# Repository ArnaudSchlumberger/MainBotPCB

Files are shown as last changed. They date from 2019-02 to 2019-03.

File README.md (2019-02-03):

# MainBotPCB

This project is part of Robot Télécom Strasbourg's work as part of our participation to the French Robot Cup.

See our Github page here: https://github.com/AssociationRobotTelecomStrasbourg

And our website (quite empty yet :/ ) here :https://associationrobottelecomstrasbourg.github.io/

MainBotPCB is the PCB that will contain the majority of the  components and connections required for our main robot to work, hence the original name :) .

NotesConception.md contains my notes while working on this project (in French)

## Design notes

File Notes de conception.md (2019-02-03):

##Cahier des charges 

##Carte de contrôle robot principal

Liste rapide des impératifs :

Accueillir carte Teensy 3.6

Maintenir une flexibilité sur la carte :

    • Pins femelle pour la Teensy
    
Communication avec d’autres composants :

    • Bus i2c
    
        ◦ Encodeurs
        
        ◦ Communication avec plusieurs composants (capteurs)
        
            ▪ Multiplexeur
            
Alimentation :

    • Régulateur 3,3V : pour Teensy et pour les composants
    
Connexion à Raspberry Pi : quelles informations ?

Ascenseur : Moteurs pas à pas 

Drivers moteurs :

https://www.robotshop.com/eu/fr/controleur-un-moteur-13a-5-a-30v-cytron.html

Datasheet :https://www.robotshop.com/media/files/pdf2/cyt-132-v2.3.pdf

Pilotés directement par PWM par la Teensy.

Encodeurs :

Communication par bus I2C

Servomoteurs/Moteurs pas à pas :

	Comment communiquer avec ? 
	
		→ PWM

Branchement Teensy en SMD :

Avec des headers males soudés sur les connexions SMD :

https://www.molex.com/molex/products/datasheet.jsp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

Cette série de headers est la bonne.

Avec des pogos :

Il faut s’assurer que les hauteurs soient bonnes pour avoir des bons contacts.

Avec ces pogos :https://www.mouser.fr/datasheet/2/273/009.1-1022823.pdf

Il faut réduire la hauteur des headers femelles, d’où :
Headers femelles : 

	Schematics https://www.molex.com/pdm_docs/sd/448120024_sd.pdf 
	
	Datasheet :https://www.mouser.fr/datasheet/2/276/0448120024_PCB_RECEPTACLES-146024.pdf
	
	Shop link:https://www.mouser.fr/ProductDetail/Molex/44812-0024?qs=sGAEpiMZZMs%252bGHln7q6pmxAVkKtOEC39IGv%2fKV14Mac%3d

Communication entre microcontrôleurs et autres trucs :

	Le robot sera embarqué d’une R.Pi qui s’occupera de la vision. Comment échanger les informations entre les deux ? En considérant la Teensy comme le Master de tout le robot, il faut configurer la R.Pi en Slave. 
Une piste ici : https://raspberrypi.stackexchange.com/questions/76109/raspberry-as-an-i2c-slave
Étendons la question à l’ensemble des composants du robot : La Teensy doit-elle contrôler l’ensemble du robot directement et simultanément, ou bien utiliser un ensemble de Slaves I2C ?
Teensy un peu overkill pour un simple chef d’orchestre ?
L’idée est à tester : communication entre deux Arduinos et commande de l’une par une autre.

Attention à la compatibilité des niveaux logiques d’un microcontrôleur à un autre :

	Pour une Arduino, la tension de niveau haut logique est de 5V, alors que celle-ci est de 3.3V pour une Rpi. Une Arduino comprend le 3.3V, mais il est dangereux de communiquer en 5V avec la Rpi. Il faut donc effectuer une conversion de niveaux logiques de bus I2C.

Il existe des convertisseurs de niveaux logiques, petite vidéo :https://www.youtube.com/watch?v=7N1shxJ8k7I

Mais on peut se contenter d’utiliser une diode Zener en inverse pour limiter la tension de communication à 3.3V. Cette diode (1N4728) pourrait faire l’affaire: https://components101.com/sites/default/files/component_datasheet/3.3V-Zener-Diode-1N4728A-datasheet.pdf

Communication I2C Arduino/Arduino :
https://www.instructables.com/id/I2C-between-Arduinos/

Ressources :
I2C :
https://www.youtube.com/watch?v=N0YtIzGIW4k
Teensy KiCAD library :
https://github.com/XenGi/teensy_library (schematics)
https://github.com/XenGi/teensy.pretty (footprints)
Teensy pins picture :
https://www.pjrc.com/teensy/card9a_rev1.png

Shop :
Pogo pins :https://www.cfeconn.com/connector/2-54mm-pogo-pin-spring-2-pin-smd-connector-supply
Multiplexeur :https://www.amazon.fr/s/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
https://learn.adafruit.com/adafruit-tca9548a-1-to-8-i2c-multiplexer-breakout/overview

end

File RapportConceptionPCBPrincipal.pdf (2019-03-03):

### Rapport de conception Carte mère Robot Principal

Les passages en rouge concernent les aspects qui sont encore incomplets.
Introduction :
Le but de ce document est de récapituler l’avancement de ce projet, ainsi que de justifier mes choix de conception. Il s’agira a posteriori de revenir sur ces choix afin d’en tirer des conclusions utiles pour la suite des projets. Ce document permettra avant tout de garder une trace des réflexions et questions qui se sont posées lors de la conception.

Pour replacer le contexte, il s’agit de concevoir la carte mère du robot principal de RTS pour la Coupe de Robotique 2019, en Belgique puis en France. N’ayant quasi aucun des composants qui seront utilisés sur la carte, ni beaucoup d’expérience dans les technologies utilisées, il a fallu avancer à tâtons. Le projet a commencé en janvier 2019, et rien du robot n’avait été conçu, le cahier des charges est donc très peu développé, ce qui justifie notre choix de garder un maximum de flexibilité en multipliant les ajouts de composants et de connexions afin de garder un maximum de degré de liberté une fois le circuit entre les mains.

Teensy 3.6 :
Il s’agit de la carte de développement choisie pour piloter tout le robot. Pourvue d’un processeur ARM 180 MHz (Contre 16 MHz pour l’ATmega 2560 d’une Arduino Mega), elle s’utilise exactement comme une Arduino standard. Toutes les entrées digitales peuvent servir d’entrée d’interruption. J’ai ajouté deux rangées de connecteurs reliées aux pins latérales de la carte, pour remplir l’objectif de flexibilité.
Ressources :
Specs :https://www.pjrc.com/teensy/techspecs.html
Pinout : https://www.pjrc.com/teensy/pinout.html
Datasheet microcontrôleur: https://www.pjrc.com/teensy/K66P144M180SF5RMV2.pdf

Alimentation :
La Teensy n’acceptant qu’une alimentation de 3.3V, la régulation se fait par un régulateur tout à fait standard. Afin d’assurer la sécurité du montage, des condensateurs au Tantalum doivent être ajoutés. Ajouter modèle régulateur choisi.

Raspberry Pi :
Non apparente sur les schémas, la Raspberry Pi se chargera de gérer la caméra et le Lidar du robot. Elle doit donc échanger avec la Teensy. La communication I2C entre les deux est théoriquement possible, mais il est complexe de configurer la Raspberry Pi en esclave I2C (cela dépend largement de la version de la R.Pi, et la documentation est pas toujours facile à trouver). Nous avons donc opté pour une communication Série (alias UART) entre les deux. Puisque les niveaux logiques des deux appareils sont égaux à 3.3V, aucune adaptation de tension logique n’est à effectuer, il suffit d’assurer les branchements RX/TX.
Des documents sur le bus Série seront rédigés pour les formations.

Bus I2C :
Certains composants, notamment les modules encodeurs magnétiques (AS5601) sont censés communiquer avec la Teensy par bus I2C. Puisqu’ils ont tous la même adresse I2C, et qu’on en utilise deux, il est nécessaire d’utiliser un multiplexeur I2C pour permettre de les utiliser. On utilisera le TCA9548A, multiplexeur 1 vers 8. Celui-ci contient déjà des résistances de pull-up égales à 10kR du côté du master (donc Teensy), mais je garde la possibilité de les améliorer en posant des résistances externes au multiplexeur. En revanche, il n’en est rien du côté des esclaves, c’est pour cela qu’elles sont également ajoutées.
Par exemple, les SDA et SCL des encodeurs AS5601sont en drain ouvert, et nécessitent donc l’ajout de résistances de pull-up. Les premiers tests concluants ont été réalisés avec des résistances de valeur 4.7kR. Un accès au canal I2C hors multiplexeur est également disponible.
En sortie du multiplexeur, pour s’assurer d’une bonne transmission logique, le GND et Vcc (3.3V) sont ajoutés pour les tensions de référence.
« The device offers an active-low [/inverted] RESET » : il faut ajouter une résistance de pull-up pour empêcher le RESET en fonctionnement nominal.
[cf p.15, 9.5.4 & p.18, 10.2 : Typical Application]
Borne connectée à la Teensy (A13, pin 32).

Des documents sur le bus I2C seront rédigés pour les formations.

Lien Multiplexeur (Breakout) : https://learn.adafruit.com/adafruit-tca9548a-1-to-8-i2c-multiplexer-breakout/overview Datasheet TCA9548A :
https://cdn-shop.adafruit.com/datasheets/tca9548a.pdf

Drivers Moteurs Pas à Pas :

Pins de mode en pull-up 100kΩ : ne pas brancher → niveau logique 1.
Le DRV8825 est un microstepping driver, il permet donc de réduire la taille d’un pas de moteur pas à pas. Cette fonctionnalité est accessible en touchant aux broches de mode, M0, M1 et M2, voir le tableau de correspondance sur le lien en-dessous. Ces bornes sont en pull-down, donc en niveau bas si non branchées.
« The resolution (step size) selector inputs (MODE0, MODE1, and MODE2) enable selection from the six step resolutions according to the table below. All three selector inputs have internal 100kΩ pull-down resistors, so leaving these three microstep selection pins disconnected results in full-step mode. » (D’après lien en fin de paragraphe). Confirmé par le datasheet du DRV8825 [https://www.pololu.com/file/0J590/drv8825.pdf, p.3, Pin Functions tab]
Il s’agit donc de se garder la possibilité de connecter les bornes à VCC via des jumpers, d’où pour chaque drivers les connecteurs 3x2.
Les bornes ENABLE sont inversées et reliées à des résistances de pull-down. Le driver est donc actif lorsque ENABLE est à niveau bas, ce qui est toujours le cas avec la résistance de pull-down. On va utiliser des cavaliers de la même manière que pour les modes, pour pouvoir éventuellement relier ces ENABLE à Vcc et désactiver les drivers.
(cf « Disabling pins » sur schéma)
Sleep et Reset connectés à Vcc (+3.3V), car comme il s’agit de bornes inversées, on les désactive ainsi.
24 à 27 en DIR, puis 28 à 31 en STP.

Fault connectés à des connecteurs JST, pour récupérer le signal pour des LEDs extérieures à la carte mère. Puisque le niveau de ces sorties est inversé, ie Haut quand il n’y a pas de probème, et bas quand il y en a, les LEDs seront allumées en état nominal.
Lien DRV8825 :
https://www.pololu.com/product/2133

Drivers Moteurs DC :
Le drivers choisis sont les MD10C de Cytron Technologies.
Capables de délivrer des courants très élevés, il suffit de deux connexions à la Teensy pour les utiliser (DIR pour la direction, et PWM pour la vitesse).
Les branchements pour quatre drivers sont présents sur la carte, deux sont dédiées au roues de la base roulante, les deux autres laissées si le besoin se fait finalement sentir.
Lien des drivers :
https://www.robotshop.com/eu/fr/controleur-un-moteur-13a-5-a-30v-cytron.html

Choix des pins de connexion Teensy/Composants :
Il est tentant de se dire qu’il importe peu de brancher la plupart des composants à des endroits bien précis de la carte, tant qu’ils assurent la bonne fonction. D’autant plus que les E/S sont nombreuses sur la Teensy. Mais à partir du moment où beaucoup de fonctions communes à certaines E/S sont utilisées, le choix est beaucoup moins simple. S’assurer que les PWM utilisés ne sont pas également les connexions du bus Série ou I2C, par exemple, est un détail évident mais à ne surtout pas oublier. Il convient de prioriser les E/S les plus rares, comme celles des bus I2C, au détriment des plus nombreuses, comme les PWM.
La quantité de pins analogiques est suffisamment grande pour se permettre d’en utiliser à d’autres fins, à savoir 22 sur la face supérieures, facilement accessibles. C’est pour cela que les broches d’adresse du multiplexeur, ainsi que les broches de direction des drivers DC sont branchés sur les bornes A0 à A6.

Affichage :
À l’instar d’une Arduino, placer des LEDs de debug sur la carte mère.
+LED d’état d’alimentation
A faire

Accès E/S inférieures de la Teensy :
Les infos sont recueillies, reste à rédiger

Dynamixel :
Ajout d’un canal Série entre la série et le réseau de Dynamixel. La Raspberry Pi s’occupera des Dynamixels.

Les prochaines parties sont peu importantes, car reflètent simplement la flexibilité visée pour la carte :

SPI :
Deux blocs de connexion pouvant assurer l’utilisation de bus SPI sont mis à disposition.

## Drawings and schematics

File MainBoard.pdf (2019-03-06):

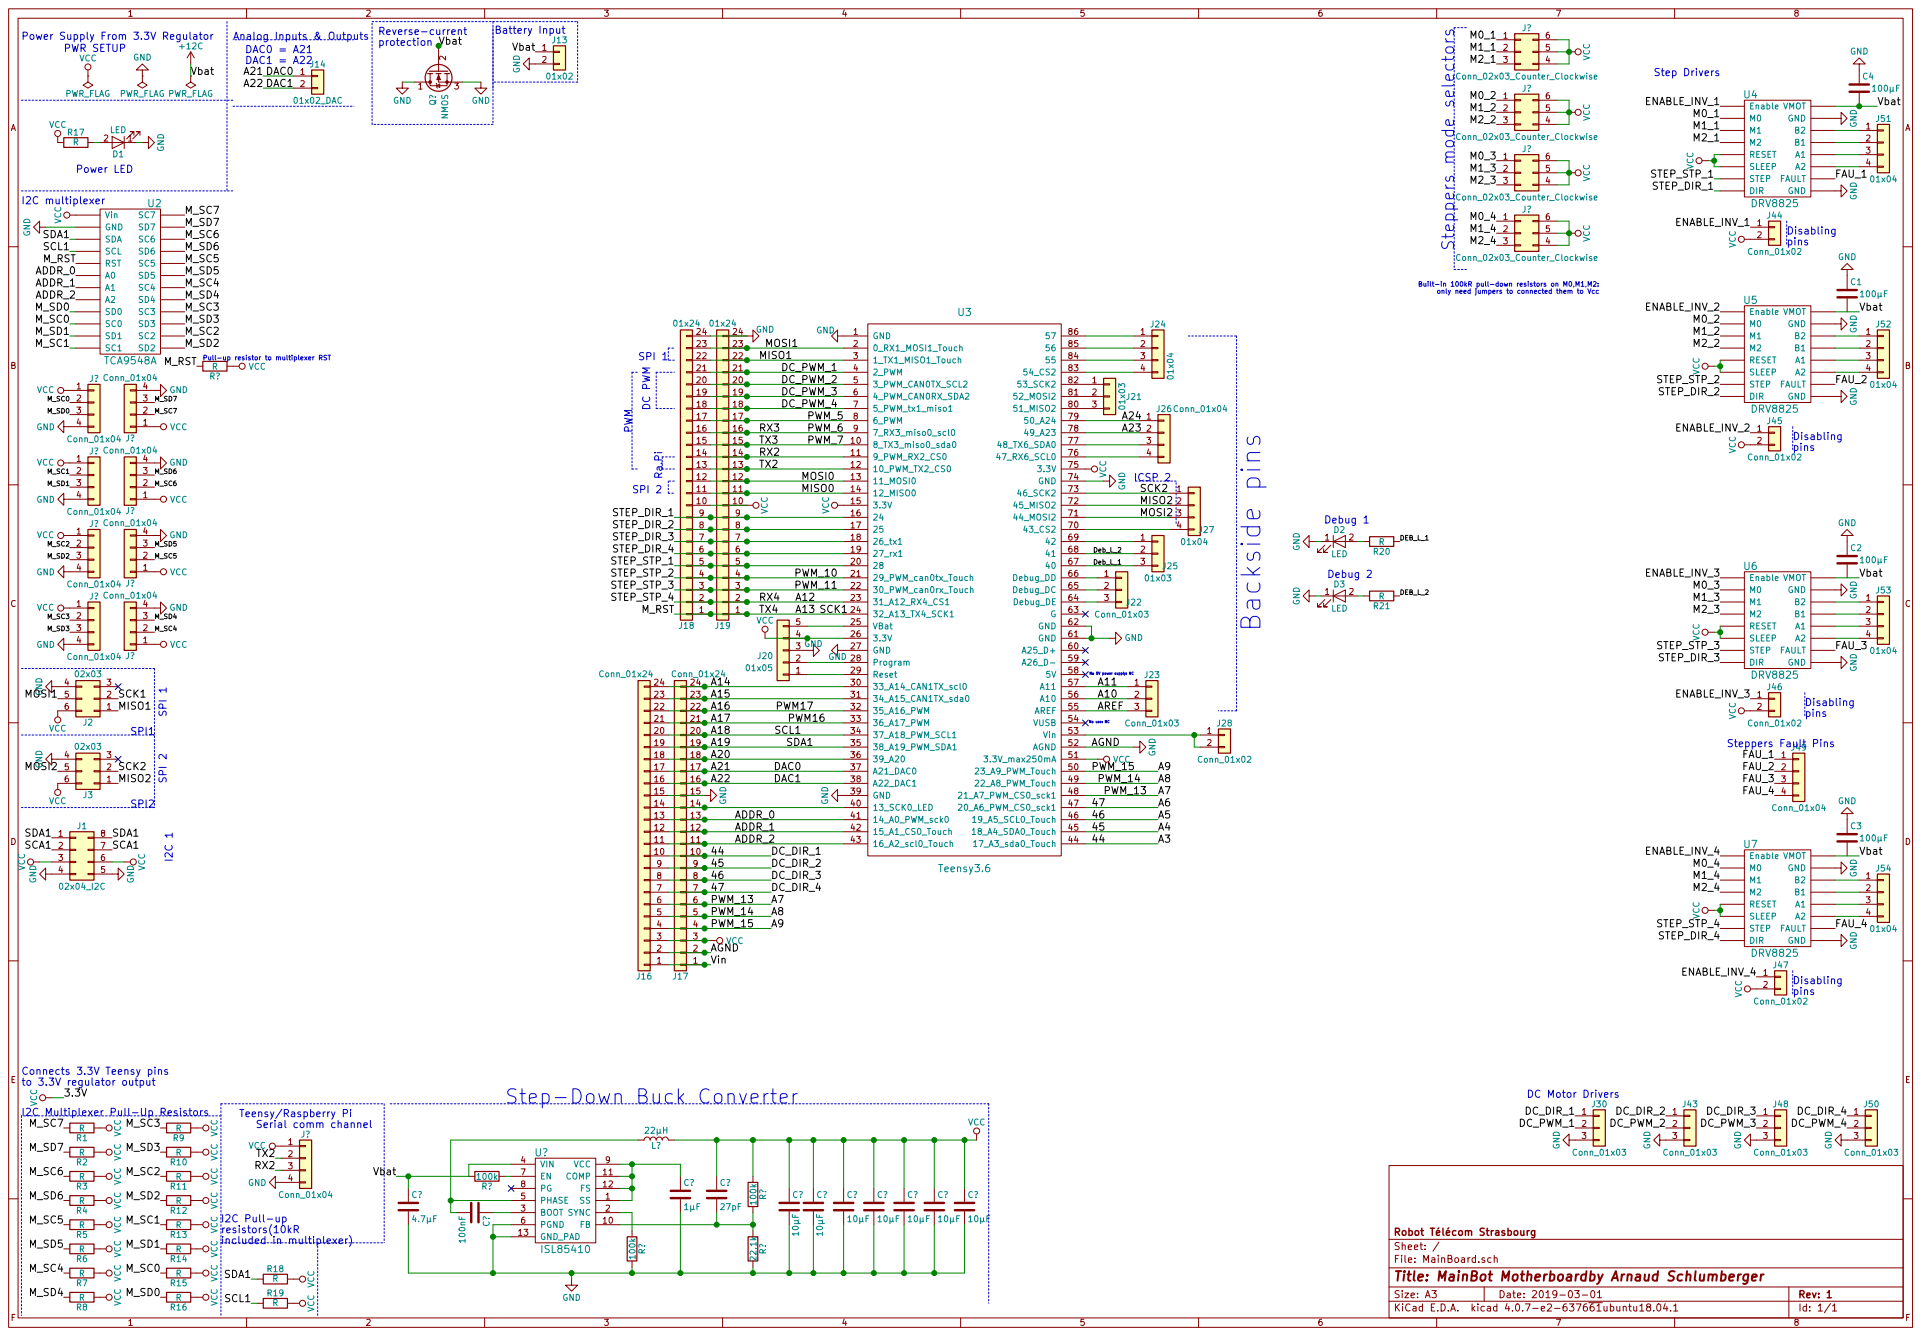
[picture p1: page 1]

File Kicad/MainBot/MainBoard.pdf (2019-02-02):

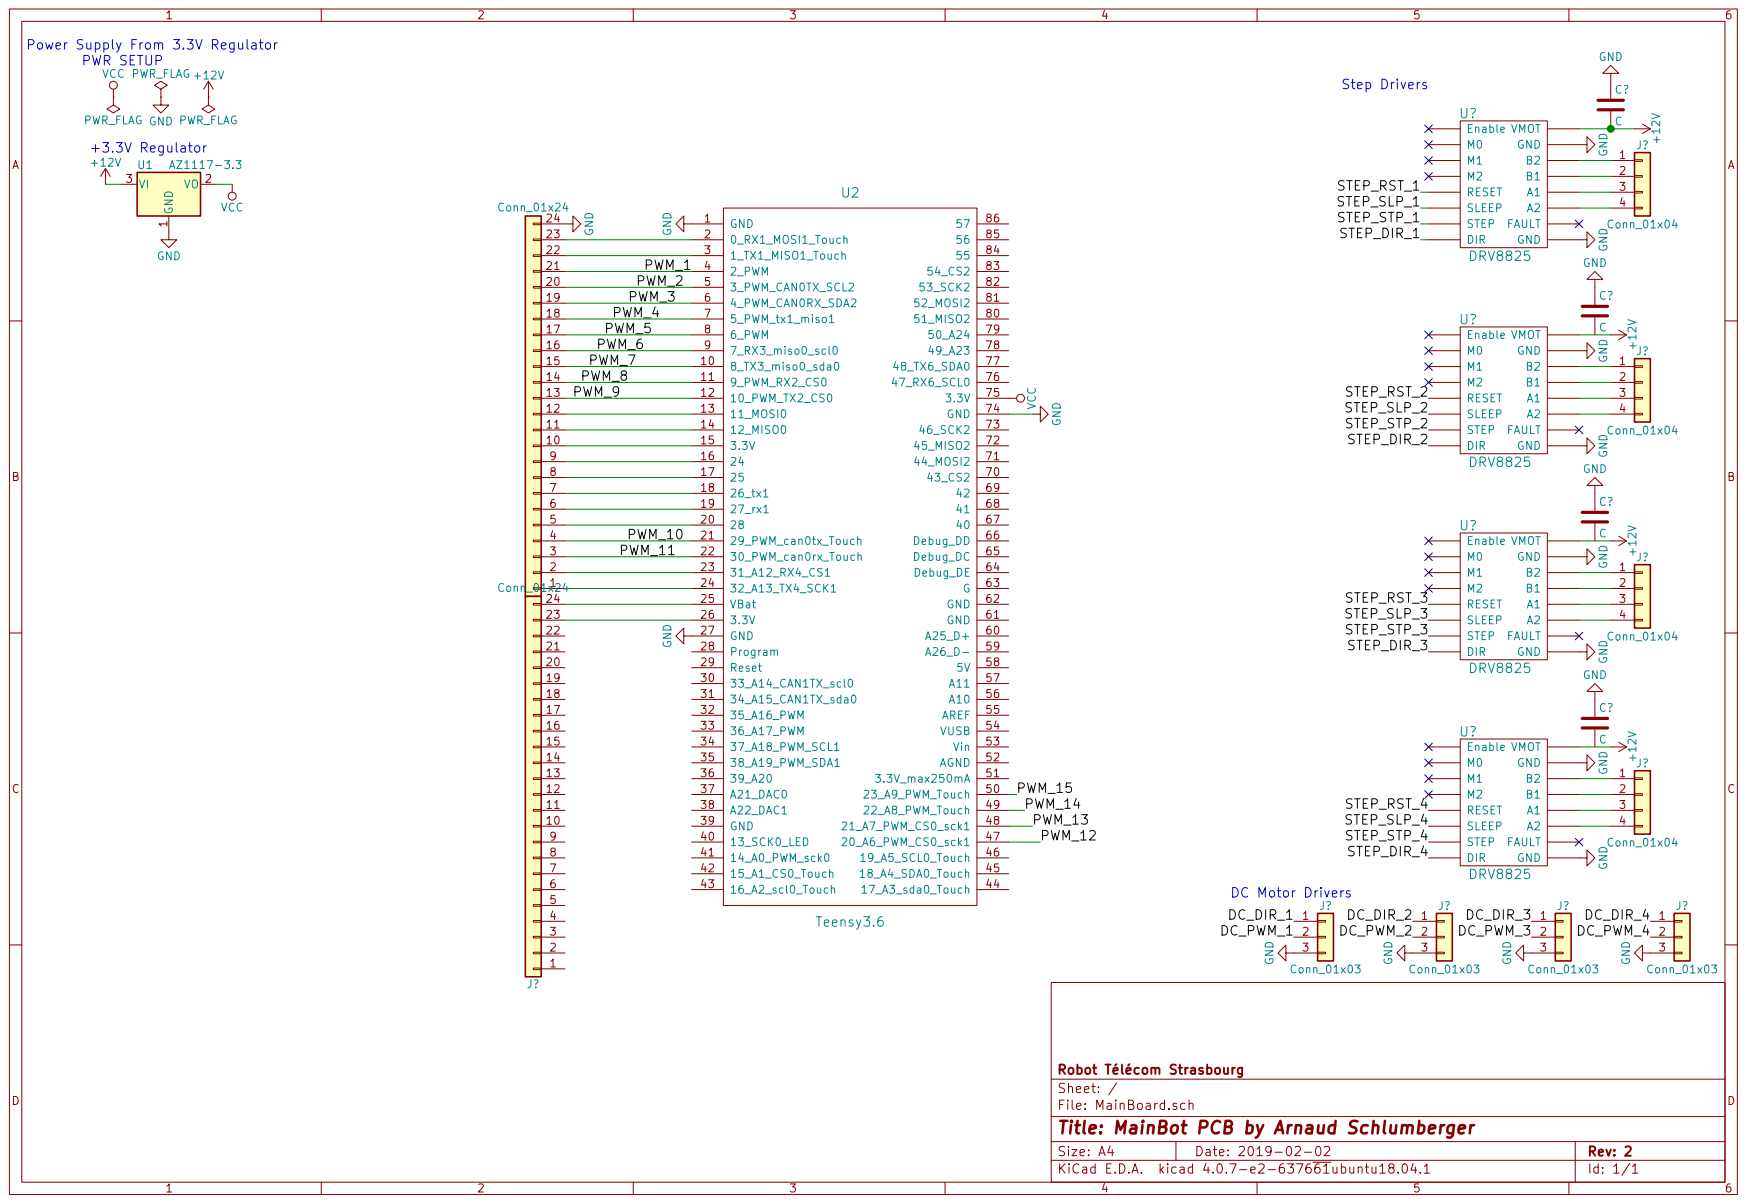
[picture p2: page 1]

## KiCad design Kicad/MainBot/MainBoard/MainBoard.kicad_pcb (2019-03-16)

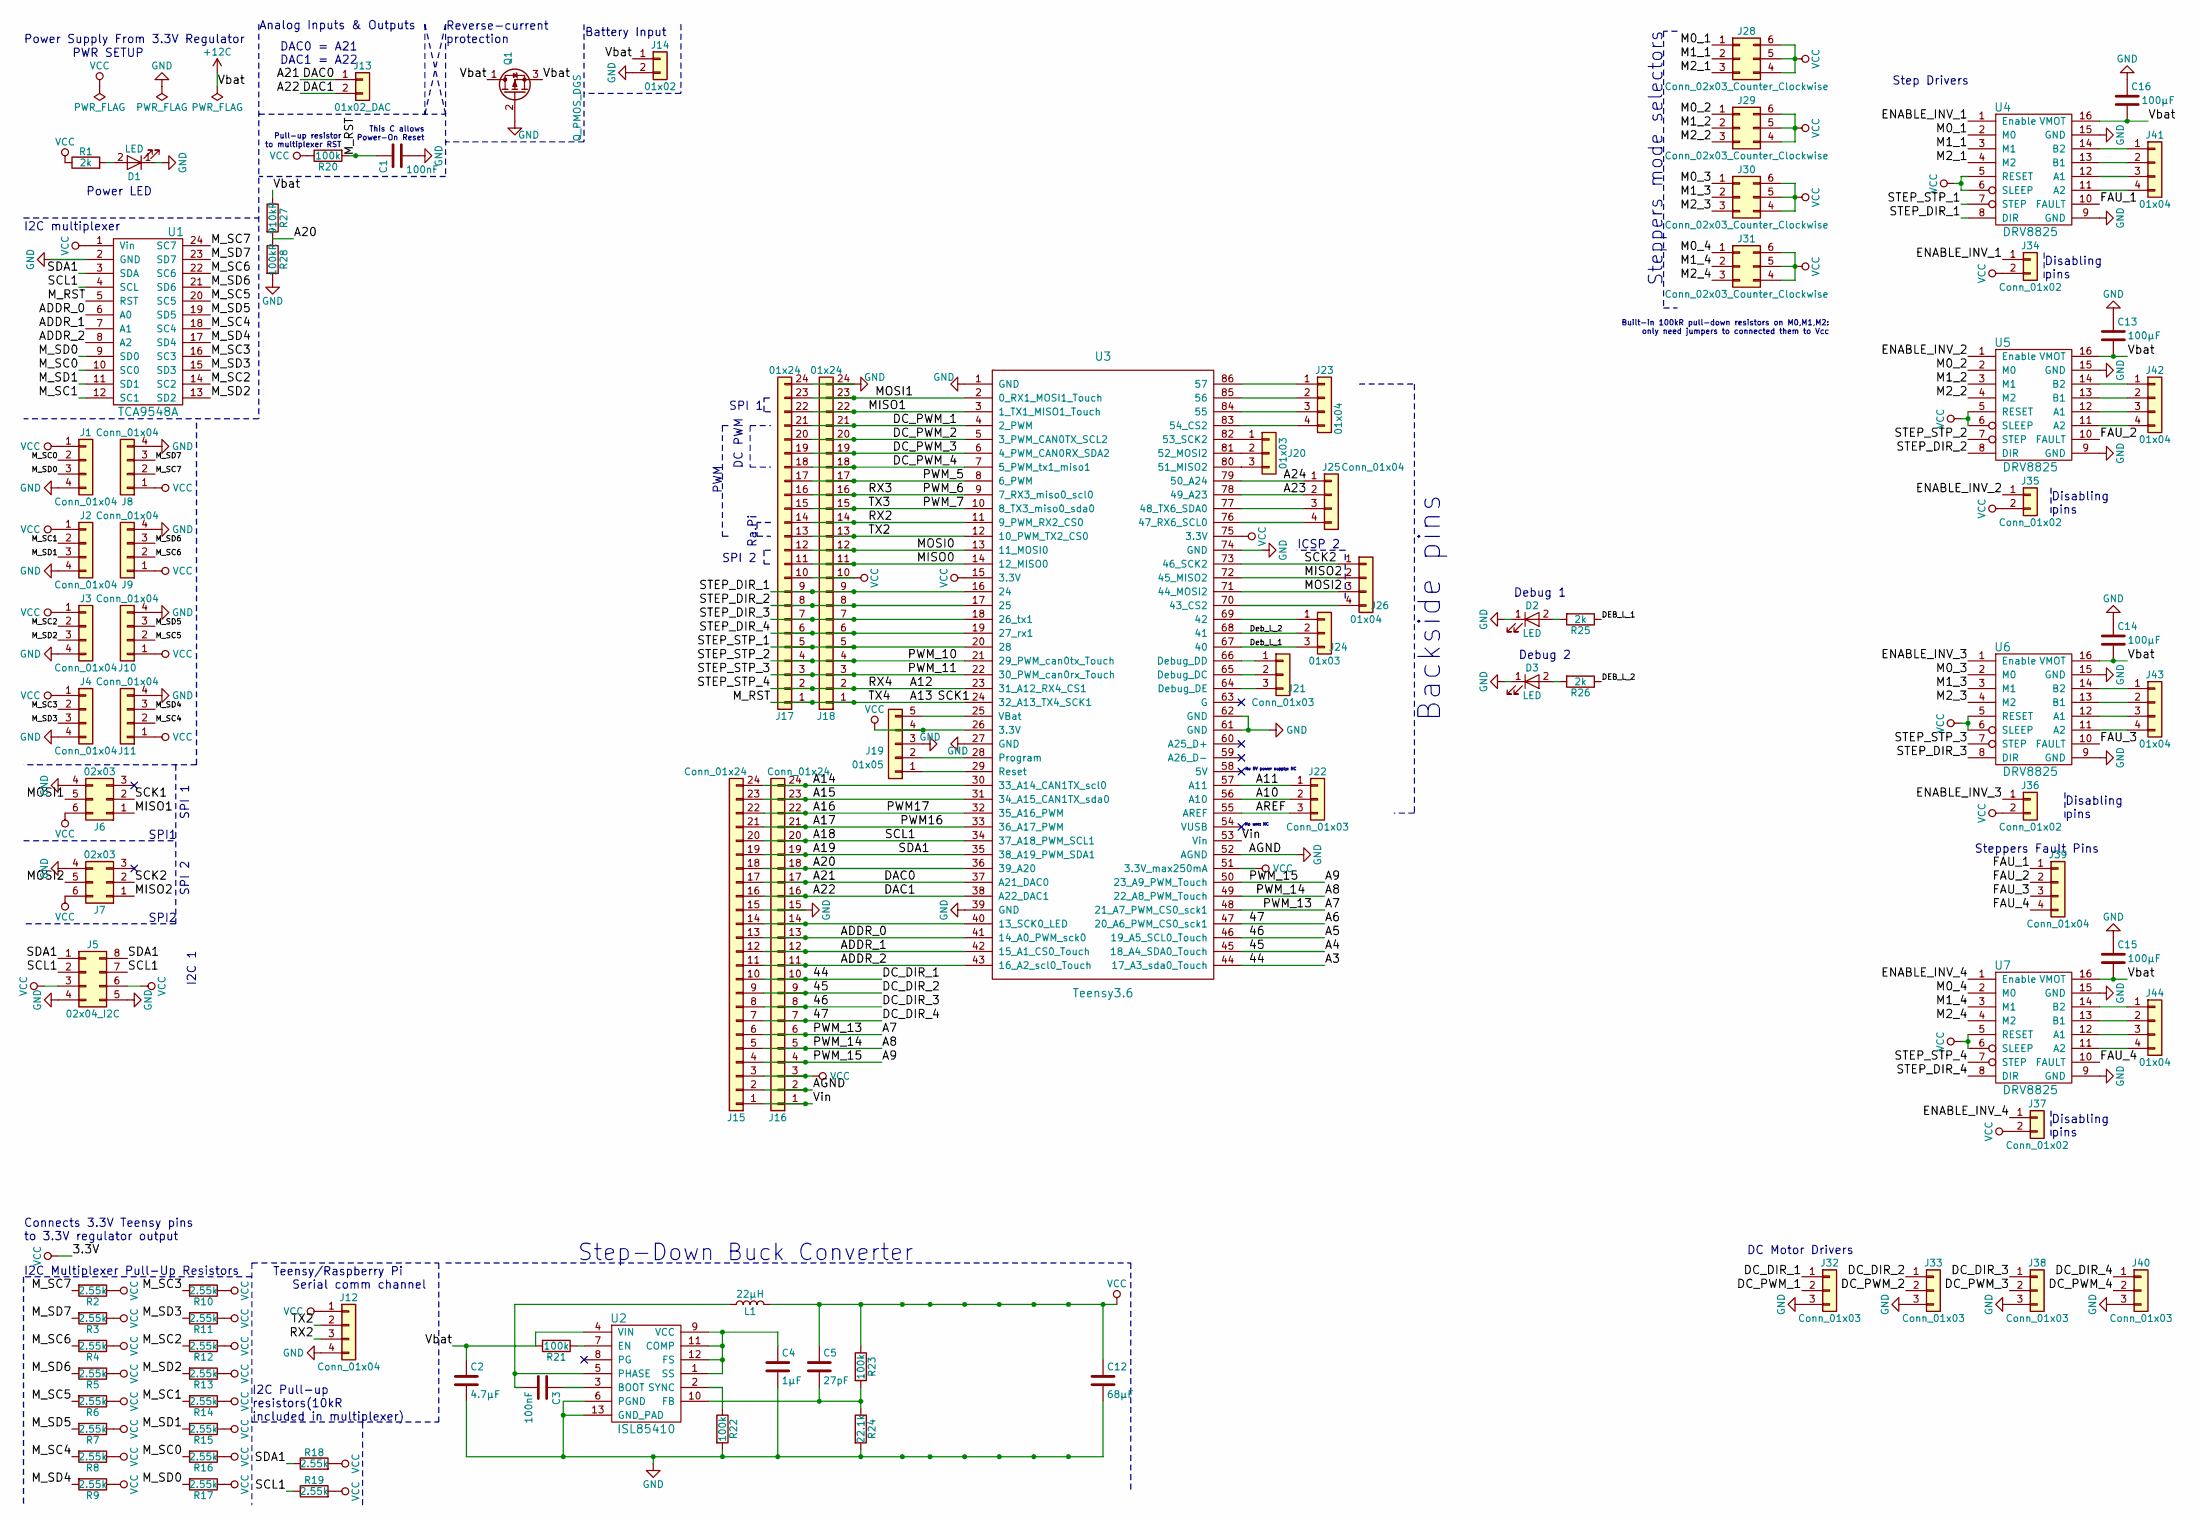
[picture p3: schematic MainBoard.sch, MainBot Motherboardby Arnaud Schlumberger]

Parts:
C1, C3: 100nF; C_1206_HandSoldering
C2: 4.7µF; C_1206_HandSoldering
C4: 1µF; C_1206_HandSoldering
C5: 27pF; C_1206_HandSoldering
C12: 68µF; CP_Elec_6.3x7.7
C13, C14, C15, C16: 100µF; CP_Radial_D6.3mm_P2.50mm
D1, D2, D3: LED; LED_1206
J1, J2, J3, J4, J8, J9, J10, J11, J12, J39: Conn_01x04; JST_XH_B04B-XH-A_04x2.50mm_Straight
J5: 02x04_I2C; Pin_Header_Straight_2x04_Pitch2.54mm
J6, J7: 02x03; Pin_Header_Straight_2x03_Pitch2.54mm
J13: 01x02_DAC; Pin_Header_Straight_1x02_Pitch2.54mm
J14: 01x02; BatConn
J15, J16: Conn_01x24; Socket_Strip_Straight_1x24_Pitch2.54mm
J17, J18: 01x24; Socket_Strip_Straight_1x24_Pitch2.54mm
J19: 01x05; Pin_Header_Straight_1x05_Pitch2.54mm
J20, J24: 01x03; Pin_Header_Straight_1x03_Pitch2.54mm
J21, J22: Conn_01x03; Pin_Header_Straight_1x03_Pitch2.54mm
J23, J26: 01x04; Pin_Header_Straight_1x04_Pitch2.54mm
J25: Conn_01x04; Pin_Header_Straight_1x04_Pitch2.54mm
J28, J29, J30, J31: Conn_02x03_Counter_Clockwise; Pin_Header_Straight_2x03_Pitch2.54mm
J32, J33, J38, J40: Conn_01x03; JST_XH_B03B-XH-A_03x2.50mm_Straight
J34, J35, J36, J37: Conn_01x02; Pin_Header_Straight_1x02_Pitch2.54mm
J41, J42, J43, J44: 01x04; JST_XH_B04B-XH-A_04x2.50mm_Straight
L1: 22µH; L1
Q1: Q_PMOS_DGS; SOT-23
R1, R25, R26: 2k; R_1206_HandSoldering
R2, R3, R4, R5, R6, R7, R8, R9, R10, R11, R12, R13, R14, R15, R16, R17, R18, R19: 2.55k; R_0805_HandSoldering
R20, R21, R22, R23: 100k; R_1206_HandSoldering
R24: 22.1k; R_1206_HandSoldering
R27: 910kR; R_1206_HandSoldering
R28: 100kR; R_1206_HandSoldering
U1: TCA9548A; TCA9548A_TSSOP
U2: ISL85410; DFN-12_DE-M
U3: Teensy3.6; Teensy35_36
U4, U5, U6, U7: DRV8825

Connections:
+12C: C2.1, C13.2, C14.2, C15.2, C16.2, J14.1, Q1.1 (D), Q1.3 (S), R21.2, R27.1, U2.4 (VIN), U4.16 (VMOT), U5.16 (VMOT), U6.16 (VMOT), U7.16 (VMOT)
/44: J15.10, J16.10, J32.1, U3.44 (17_A3_sda0_Touch)
/45: J15.9, J16.9, J33.1, U3.45 (18_A4_SDA0_Touch)
/46: J15.8, J16.8, J38.1, U3.46 (19_A5_SCL0_Touch)
/47: J15.7, J16.7, J40.1, U3.47 (20_A6_PWM_CS0_sck1)
/A7: J15.6, J16.6, U3.48 (21_A7_PWM_CS0_sck1)
/A8: J15.5, J16.5, U3.49 (22_A8_PWM_Touch)
/A9: J15.4, J16.4, U3.50 (23_A9_PWM_Touch)
/A10: J22.2, U3.56 (A10)
/A11: J22.1, U3.57 (A11)
/A12: J17.2, J18.2, U3.23 (31_A12_RX4_CS1), U7.7 (STEP)
/A13: C1.1, J6.2, J17.1, J18.1, R20.2, U1.5 (RST), U3.24 (32_A13_TX4_SCK1)
/A14: J15.24, J16.24, U3.30 (33_A14_CAN1TX_scl0)
/A15: J15.23, J16.23, U3.31 (34_A15_CAN1TX_sda0)
/A16: J15.22, J16.22, U3.32 (35_A16_PWM)
/A17: J15.21, J16.21, U3.33 (36_A17_PWM)
/A18: J5.2, J5.7, J15.20, J16.20, R19.1, U1.4 (SCL), U3.34 (37_A18_PWM_SCL1)
/A19: J5.1, J5.8, J15.19, J16.19, R18.1, U1.3 (SDA), U3.35 (38_A19_PWM_SDA1)
/A20: J15.18, J16.18, R27.2, R28.1, U3.36 (39_A20)
/A21: J13.1, J15.17, J16.17, U3.37 (A21_DAC0)
/A22: J13.2, J15.16, J16.16, U3.38 (A22_DAC1)
/A23: J25.2, U3.78 (49_A23)
/A24: J25.1, U3.79 (50_A24)
/ADDR_0: J15.13, J16.13, U1.6 (A0), U3.41 (14_A0_PWM_sck0)
/ADDR_1: J15.12, J16.12, U1.7 (A1), U3.42 (15_A1_CS0_Touch)
/ADDR_2: J15.11, J16.11, U1.8 (A2), U3.43 (16_A2_scl0_Touch)
/AREF: J22.3, U3.55 (AREF)
/DC_PWM_1: J17.21, J18.21, J32.2, U3.4 (2_PWM)
/DC_PWM_2: J17.20, J18.20, J33.2, U3.5 (3_PWM_CAN0TX_SCL2)
/DC_PWM_3: J17.19, J18.19, J38.2, U3.6 (4_PWM_CAN0RX_SDA2)
/DC_PWM_4: J17.18, J18.18, J40.2, U3.7 (5_PWM_tx1_miso1)
/DEB_L_1: J24.3, R25.1, U3.67 (40)
/DEB_L_2: J24.2, R26.1, U3.68 (41)
/ENABLE_INV_1: J34.1, U4.1 (Enable)
/ENABLE_INV_2: J35.1, U5.1 (Enable)
/ENABLE_INV_3: J36.1, U6.1 (Enable)
/ENABLE_INV_4: J37.1, U7.1 (Enable)
/FAU_1: J39.1, U4.10 (FAULT)
/FAU_2: J39.2, U5.10 (FAULT)
/FAU_3: J39.3, U6.10 (FAULT)
/FAU_4: J39.4, U7.10 (FAULT)
/M0_1: J28.1, U4.2 (M0)
/M0_2: J29.1, U5.2 (M0)
/M0_3: J30.1, U6.2 (M0)
/M0_4: J31.1, U7.2 (M0)
/M1_1: J28.2, U4.3 (M1)
/M1_2: J29.2, U5.3 (M1)
/M1_3: J30.2, U6.3 (M1)
/M1_4: J31.2, U7.3 (M1)
/M2_1: J28.3, U4.4 (M2)
/M2_2: J29.3, U5.4 (M2)
/M2_3: J30.3, U6.4 (M2)
/M2_4: J31.3, U7.4 (M2)
/MISO0: J17.11, J18.11, U3.14 (12_MISO0)
/MISO1: J6.1, J17.22, J18.22, U3.3 (1_TX1_MISO1_Touch)
/MISO2: J7.1, J26.2, U3.72 (45_MISO2)
/MOSI0: J17.12, J18.12, U3.13 (11_MOSI0)
/MOSI1: J6.5, J17.23, J18.23, U3.2 (0_RX1_MOSI1_Touch)
/MOSI2: J7.5, J26.3, U3.71 (44_MOSI2)
/M_SC0: J1.2, R16.2, U1.10 (SC0)
/M_SC1: J2.2, R14.2, U1.12 (SC1)
/M_SC2: J3.2, R12.2, U1.14 (SC2)
/M_SC3: J4.2, R10.2, U1.16 (SC3)
/M_SC4: J11.2, R8.2, U1.18 (SC4)
/M_SC5: J10.2, R6.2, U1.20 (SC5)
/M_SC6: J9.2, R4.2, U1.22 (SC6)
/M_SC7: J8.2, R2.2, U1.24 (SC7)
/M_SD0: J1.3, R17.2, U1.9 (SD0)
/M_SD1: J2.3, R15.2, U1.11 (SD1)
/M_SD2: J3.3, R13.2, U1.13 (SD2)
/M_SD3: J4.3, R11.2, U1.15 (SD3)
/M_SD4: J11.3, R9.2, U1.17 (SD4)
/M_SD5: J10.3, R7.2, U1.19 (SD5)
/M_SD6: J9.3, R5.2, U1.21 (SD6)
/M_SD7: J8.3, R3.2, U1.23 (SD7)
/PWM_5: J17.17, J18.17, U3.8 (6_PWM)
/PWM_6: J17.16, J18.16, U3.9 (7_RX3_miso0_scl0)
/PWM_7: J17.15, J18.15, U3.10 (8_TX3_miso0_sda0)
/PWM_10: J17.4, J18.4, U3.21 (29_PWM_can0tx_Touch), U5.7 (STEP)
/PWM_11: J17.3, J18.3, U3.22 (30_PWM_can0rx_Touch), U6.7 (STEP)
/RX2: J12.3, J17.14, J18.14, U3.11 (9_PWM_RX2_CS0)
/SCK2: J7.2, J26.1, U3.73 (46_SCK2)
/STEP_DIR_1: J17.9, J18.9, U3.16 (24), U4.8 (DIR)
/STEP_DIR_2: J17.8, J18.8, U3.17 (25), U5.8 (DIR)
/STEP_DIR_3: J17.7, J18.7, U3.18 (26_tx1), U6.8 (DIR)
/STEP_DIR_4: J17.6, J18.6, U3.19 (27_rx1), U7.8 (DIR)
/STEP_STP_1: J17.5, J18.5, U3.20 (28), U4.7 (STEP)
/TX2: J12.2, J17.13, J18.13, U3.12 (10_PWM_TX2_CS0)
/Vin: J15.1, J16.1, U3.53 (Vin)
GND: C1.2, C2.2, C4.2, C12.2, C13.1, C14.1, C15.1, C16.1, D1.1 (K), D2.1 (K), D3.1 (K), J1.4, J2.4, J3.4, J4.4, J5.4, J5.5, J6.4, J7.4, J8.4, J9.4, J10.4, J11.4, J12.4, J14.2, J15.2, J15.15, J16.2, J16.15, J17.24, J18.24, J19.3, J32.3, J33.3, J38.3, J40.3, Q1.2 (G), R22.2, R24.2, R28.2, U1.2 (GND), U2.6 (PGND), U2.13 (GND_PAD), U3.1 (GND), U3.27 (GND), U3.39 (GND), U3.52 (AGND), U3.61 (GND), U3.62 (GND), U3.74 (GND), U4.9 (GND), U4.15 (GND), U5.9 (GND), U5.15 (GND), U6.9 (GND), U6.15 (GND), U7.9 (GND), U7.15 (GND)
unnamed: C3.1, U2.3 (BOOT)
unnamed: C3.2, L1.1, U2.5 (PHASE)
unnamed: C4.1, U2.1 (SS), U2.9 (VCC), U2.11 (COMP), U2.12 (FS)
unnamed: C5.2, R23.2, R24.1, U2.10 (FB)
unnamed: D1.2 (A), R1.2
unnamed: D2.2 (A), R25.2
unnamed: D3.2 (A), R26.2
unnamed: J15.14, J16.14, U3.40 (13_SCK0_LED)
unnamed: J19.1, U3.29 (Reset)
unnamed: J19.2, U3.28 (Program)
unnamed: J19.5, U3.25 (VBat)
unnamed: J20.1, U3.82 (53_SCK2)
unnamed: J20.2, U3.81 (52_MOSI2)
unnamed: J20.3, U3.80 (51_MISO2)
unnamed: J21.1, U3.66 (Debug_DD)
unnamed: J21.2, U3.65 (Debug_DC)
unnamed: J21.3, U3.64 (Debug_DE)
unnamed: J23.1, U3.86 (57)
unnamed: J23.2, U3.85 (56)
unnamed: J23.3, U3.84 (55)
unnamed: J23.4, U3.83 (54_CS2)
unnamed: J24.1, U3.69 (42)
unnamed: J25.3, U3.77 (48_TX6_SDA0)
unnamed: J25.4, U3.76 (47_RX6_SCL0)
unnamed: J26.4, U3.70 (43_CS2)
unnamed: J41.1, U4.14 (B2)
unnamed: J41.2, U4.13 (B1)
unnamed: J41.3, U4.12 (A1)
unnamed: J41.4, U4.11 (A2)
unnamed: J42.1, U5.14 (B2)
unnamed: J42.2, U5.13 (B1)
unnamed: J42.3, U5.12 (A1)
unnamed: J42.4, U5.11 (A2)
unnamed: J43.1, U6.14 (B2)
unnamed: J43.2, U6.13 (B1)
unnamed: J43.3, U6.12 (A1)
unnamed: J43.4, U6.11 (A2)
unnamed: J44.1, U7.14 (B2)
unnamed: J44.2, U7.13 (B1)
unnamed: J44.3, U7.12 (A1)
unnamed: J44.4, U7.11 (A2)
unnamed: R21.1, U2.7 (EN)
unnamed: R22.1, U2.2 (SYNC)
VCC: C5.1, C12.1, J1.1, J2.1, J3.1, J4.1, J5.3, J5.6, J6.6, J7.6, J8.1, J9.1, J10.1, J11.1, J12.1, J15.3, J16.3, J17.10, J18.10, J19.4, J28.4, J28.5, J28.6, J29.4, J29.5, J29.6, J30.4, J30.5, J30.6, J31.4, J31.5, J31.6, J34.2, J35.2, J36.2, J37.2, L1.2, R1.1, R2.1, R3.1, R4.1, R5.1, R6.1, R7.1, R8.1, R9.1, R10.1, R11.1, R12.1, R13.1, R14.1, R15.1, R16.1, R17.1, R18.2, R19.2, R20.1, R23.1, U1.1 (Vin), U3.15 (3.3V), U3.26 (3.3V), U3.51 (3.3V_max250mA), U3.75 (3.3V), U4.5 (RESET), U4.6 (SLEEP), U5.5 (RESET), U5.6 (SLEEP), U6.5 (RESET), U6.6 (SLEEP), U7.5 (RESET), U7.6 (SLEEP)

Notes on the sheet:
Power Supply From 3.3V Regulator
PWR SETUP
Step Drivers
DC Motor Drivers
Teensy/Raspberry Pi Serial comm channel
I2C multiplexer
I2C Pull-up resistors(10kR included in multiplexer)
Connects 3.3V Teensy pins to 3.3V regulator output
ICSP 2
SPI2
SPI1
I2C Multiplexer Pull-Up Resistors
DAC0 = A21 DAC1 = A22
Analog Inputs & Outputs
PWM
DC PWM
Ra.Pi
SPI 1
SPI 2
SPI 1
I2C 1
Disabling pins
Power LED
Steppers Fault Pins
Debug 1
Debug 2
Backside pins
No 5V power supply: NC
No use: NC
Pull-up resistor to multiplexer RST
Built-in 100kR pull-down resistors on M0,M1,M2: only need jumpers to connected them to Vcc
Steppers mode selectors
Battery Input
Step-Down Buck Converter
This C allows Power-On Reset
Reverse-current protection

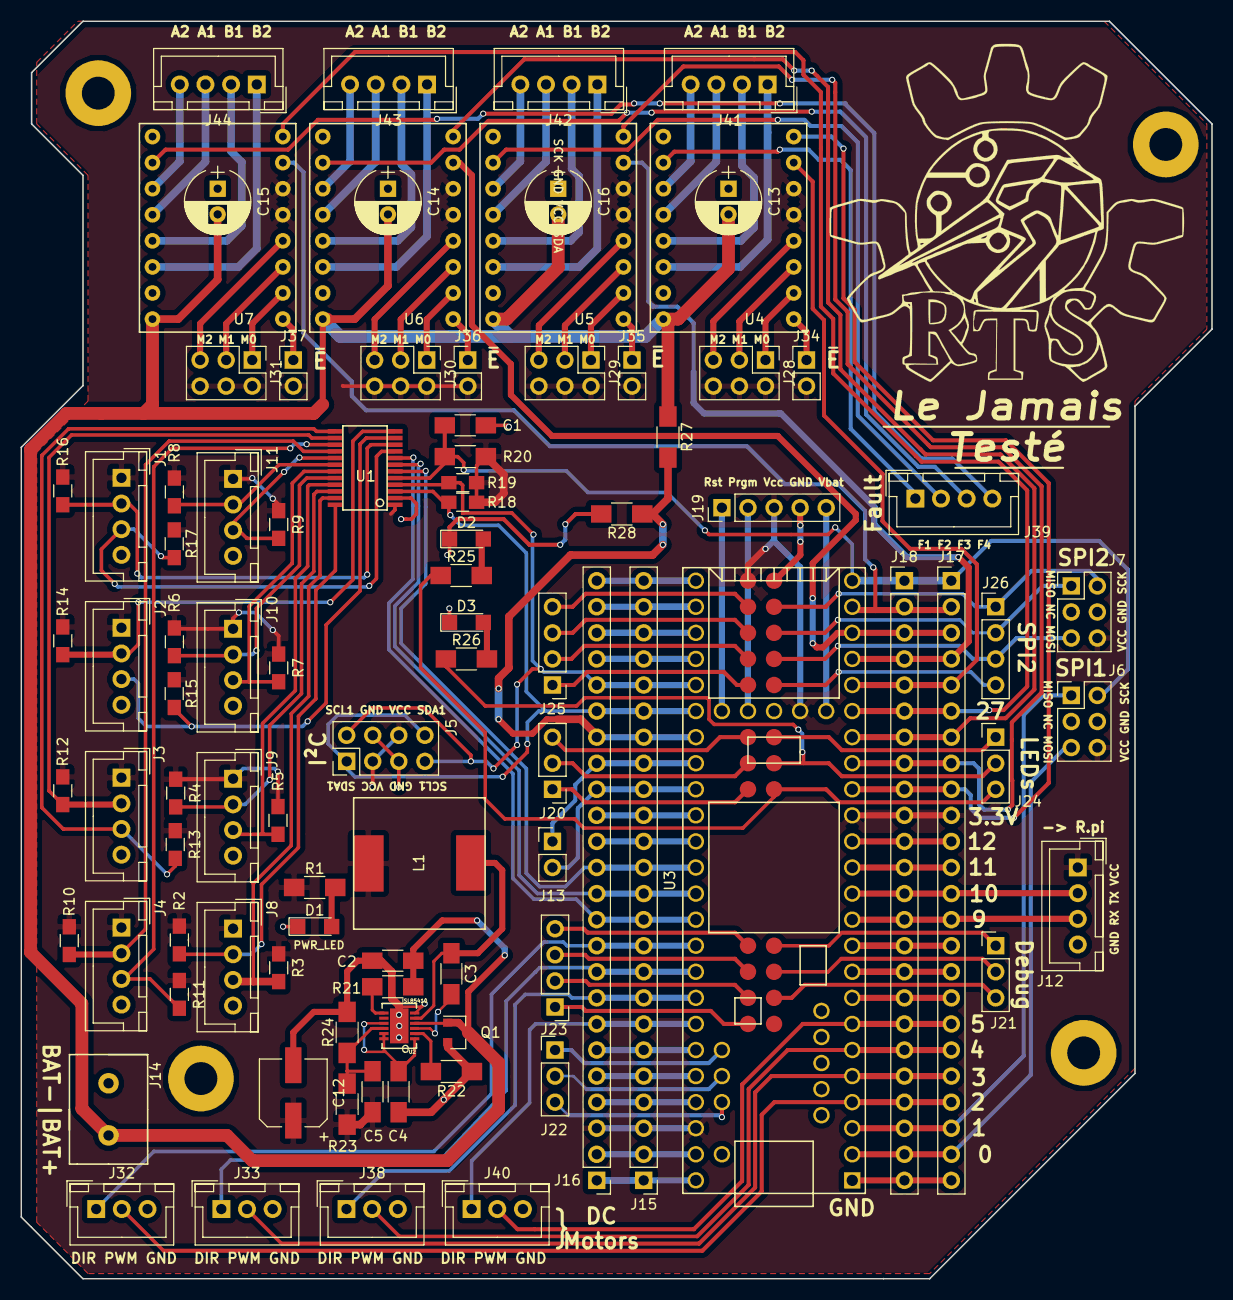
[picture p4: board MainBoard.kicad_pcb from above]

Board: 2 copper layers, 116.0 x 122.5 mm, 93 parts (0 on the bottom side), 134 nets.

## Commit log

2019-02-02 Setting everything up
    [Alim.kicad_pcb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]
2019-02-02 Cleaning things up
    [Alim.kicad_pcb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]
2019-02-02 First schematic PDF export
2019-02-02 Schematic update
2019-02-07 Ajout Comm Série Rasp/Teensy
    [MainBoard.sch]
2019-02-07 Added I2C pull-up resistor, I2C multiplexer
    [MainBoard.sch]
2019-02-11 Finished female headers
    [MainBoard.kicad_pcb, MainBoard.sch]
2019-02-11 Added multiplexer and driver footprint, updated PCB
    [MainBoard.kicad_pcb, MainBoard.sch]
2019-02-11 Added notes on schematic
    [MainBoard.sch]
2019-02-12 Added capacitors to regulator, ICSP2 pins, completed I2C Vcc and GND connections
    [MainBoard.sch]
2019-02-12 Added SPI1 and SPI2 channels
    [MainBoard.sch]
2019-02-12 Finished Multiplexer output, added pulled up resistors to multiplexer output
    [MainBoard.sch]
2019-02-12 Removed NC on DRV8825 Step drivers
    [MainBoard.sch]
2019-02-12 Removed NC on FAULT pins of Step drivers
    [MainBoard.sch]
2019-02-13 Added Analog INs and OUTs
    [MainBoard.sch]
2019-02-13 Increased Schematic Size
    [MainBoard.sch]
2019-02-16 Added stepper drivers' capacitors values
    [MainBoard.sch]
2019-02-16 Deleted PWM and analog blocks
    [MainBoard.sch]
2019-02-16 Connected TCA4598A's ADDR pins to Teensy, Connected DC Drivers' PWM pins to Teensy
    [MainBoard.sch]
2019-02-16 Switched Serial communication channel from RX1/TX1 to RX2/TX2, Deleted unused labels
    [MainBoard.sch]
2019-02-16 Connected DC drivers pins to Teensy
    [MainBoard.sch]
2019-02-20 Added mode selectors for DRV8825 in the form of jumper connectors
    [MainBoard.sch]
2019-02-20 Added jumpers to disable DRV8825 Stepper drivers
    [MainBoard.sch]
2019-02-20 Added AREF selector
    [MainBoard.sch]
2019-02-27 Connected Steppers Sleep and Reset pins to Vcc
    [MainBoard.sch]
2019-03-01 Connected Steppers STP & DIR to Teensy
    [MainBoard.sch]
2019-03-01 Added external connectors to Steppers Fault pins
    [MainBoard.sch]
2019-03-01 Added DAC0 and DAC1 labels
    [MainBoard.sch]
2019-03-01 Connected backside pins to headers
    [MainBoard.sch]
2019-03-01 Added notes
    [MainBoard.sch]
2019-03-01 Added Serial channel to Dynamixel actuators, connected debug LEDs to Teensy
    [MainBoard.sch]
2019-03-03 Removed Dynamixel connectors
    [MainBoard.sch]
2019-03-03 Redesigned Steppers' mode selectors
    [MainBoard.sch]
2019-03-03 Corrected multiplexer connectors to slaves
    [MainBoard.sch]
2019-03-03 Added pull-up resistor to multiplexer RST pin
    [MainBoard.sch]
2019-03-03 Corrected Steppers' mode selectors
    [MainBoard.sch]
2019-03-03 Connected multiplexer RST to Teensy through pin 32
    [MainBoard.sch]
2019-03-03 Corrected Rpi/Teensy Serial Channel: added VCC and GND
    [MainBoard.sch]
2019-03-03 Added Design report
    [MainBoard.sch]
2019-03-06 Corrected Reverse-current protection, replaced regulator with 3.3V Step-Down Buck Converter
    [_saved_MainBoard.sch]
2019-03-06 Updated schematic pdf
    [MainBoard.sch, _saved_MainBoard.sch]
2019-03-06 Library corrections: added pins numbers
    [MainBoard.sch]
2019-03-08 Corrections and started PCB
    [MainBoard.kicad_pcb, MainBoard.sch]
2019-03-12 So much things :)
    [MainBoard.kicad_pcb, MainBoard.sch]
2019-03-16 Small details
    [MainBoard.kicad_pcb]
